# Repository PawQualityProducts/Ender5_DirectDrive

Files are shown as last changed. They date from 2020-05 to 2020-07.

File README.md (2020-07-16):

# DirectDrive Mount for Creality Ender 5+ (5 Pro and 5)
By Paul.Haines@PawQualityProducts.co.uk

## Design Considerations
This is a Simple Direct Drive Mount originally designed for the Creality Ender 5+, but may also be compatible with the Ender 5 and Ender 5 Pro.

It was developed to:
* Improve injection of filament into the Hot-End by mounting the Extruder Drive close to the Hot-End
* Provide a more even balance for the Print-Head by utilising the Extruder Drive Stepper Motor as a counter-weight to the Hot-End assembly. This was done by making use of the space between the Print-Head Assembly and Carriage Rollers
<br/>
<b>Disclaimer</b><br/>
<i>The 3D print models, STL files, instructions etc. contained in this repository may be used freely but at your own risk.<br/> No liability will be accepted for damage or loss resulting from the use of any files or information contained in this repository.</i>

## To build the Direct Drive Mount you will need:
1. The Direct Drive Mount STL files<br/>
Two versions are available:
- <a href="https://github.com/PawQualityProducts/Ender5_DirectDrive/blob/master/DirectDriveMount_Ender5_Plus.stl">Ender 5+ version (with BLTouch)</a> <br/>
- <a href="https://github.com/PawQualityProducts/Ender5_DirectDrive/blob/master/DirectDriveMount_Ender5_NoBLTouch.stl">Ender 5x version (without BLTouch)</a> <br/>

A <a href="https://github.com/hainesyp/Ender5Plus_DirectDrive/blob/master/DirectDriveMount_Ender5_x_Guide.stl">Filament Guide</a> is also provided. <i>NB: An M3 (3mm x 20mm) bolt and nut are required to attach the Guide to the Mount</i>
<br/>
<br/>
<b><i>Build with standard settings with Full Support enabled (there's only a bit of support)</i></b><br/>
<br/>
2. <a href="https://www.amazon.co.uk/gp/product/B07SY745CF/ref=ppx_yo_dt_b_asin_title_o03_s00?ie=UTF8&psc=1">WINSINN Ender Aluminum Dual Extrusion Drive Feed</a> <br/>
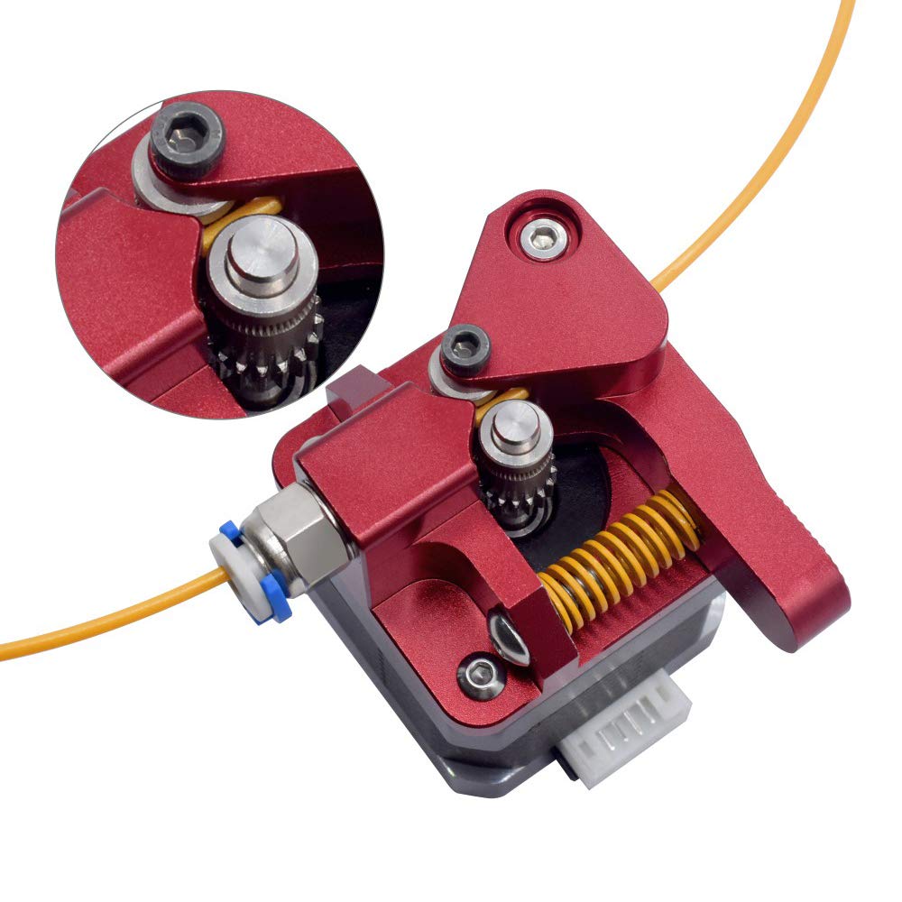
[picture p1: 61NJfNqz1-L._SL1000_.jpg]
 <br/>
<i>NB: If you are installing the WINSINN Extruder Drive Feed assembly as part of this Mod, then I recommend you install it first, and <b>re-calibrate the E-Step settings on your printer</b>, to ensure it's operating correctly before proceeding with the rest of the Mod</i>
<br/>
<br/>
3. Cable Extender ( used in Reprap 3D Printers CNC Machines): <br/>
<a href="https://www.amazon.co.uk/gp/product/B0728J6QTG/ref=ppx_yo_dt_b_asin_image_o00_s00?ie=UTF8&psc=1">UEETEK Bipolar Stepper Motor Cable for NEMA 17</a>  <br/>
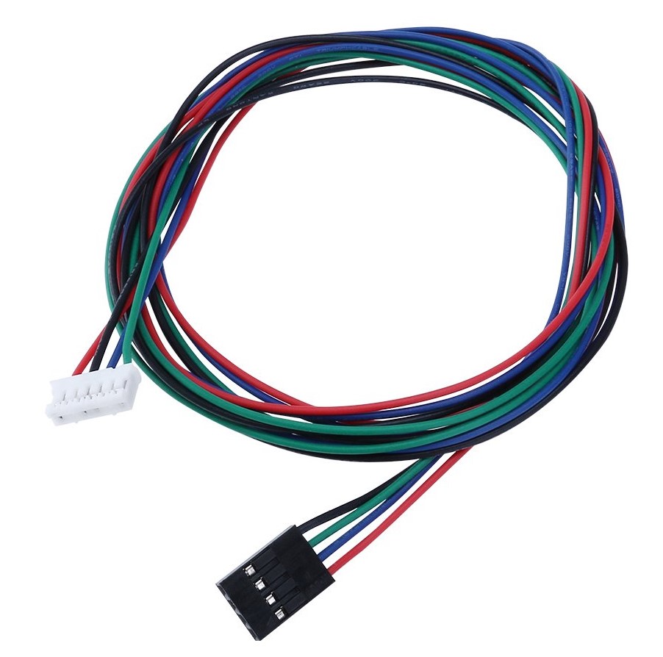
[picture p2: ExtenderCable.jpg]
 <br/>
<br/>
Additionally, I used a Male-To-Male <a href="https://www.amazon.co.uk/Elegoo-120pcs-Multicolored-Breadboard-arduino-colorful/dp/B01EV70C78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">Dupont Cable</a> to make the connection between your stepper motor cable and the extended stepper motor cable<br/>
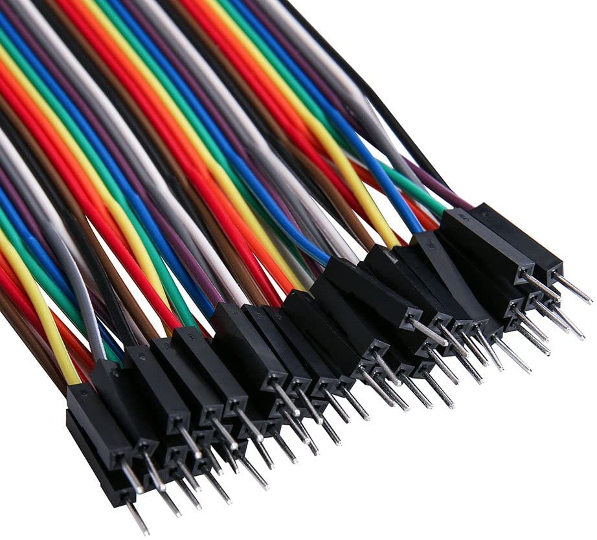
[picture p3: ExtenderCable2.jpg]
 <br/>

4. 80mm of Bowden Tube (Capricorn Tubing recommended) <br/>
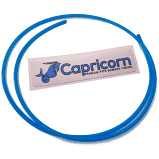
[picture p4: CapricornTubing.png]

<br/>

## To mount onto the print-head:
<table>
  <tr>
    <td>
      <h3>Step 1</h3>
      <p>Heat the Hot-End to ~190 degrees then Remove the Bowden Tube from the Hot-End</p>
    </td>
    <td>&nbsp;</td>
  </tr>
  <tr>
    <td>
      <h3>Step 2</h3>
      <p>Allow the hot-end to cool then remove the Bowden Tube Connector from the Hot-End</p>
    </td>
    <td>&nbsp;</td>
  </tr>
  <tr>
    <td>
      <h3>Step 3</h3>
      <p>Release the tension on the X Drive belt, then remove to top two rollers from the Hot-End carriage<br/>
        <i>NB: It is recommended that you position the Hot-Bed so that the Print-Head carriage can be supported while the Direct Drive Mount is attached. It's also advisable to protect your Hot-Bed surface during the mounting process (eg. especially when attaching the drive stepper motor)</i>
      </p>
    </td>
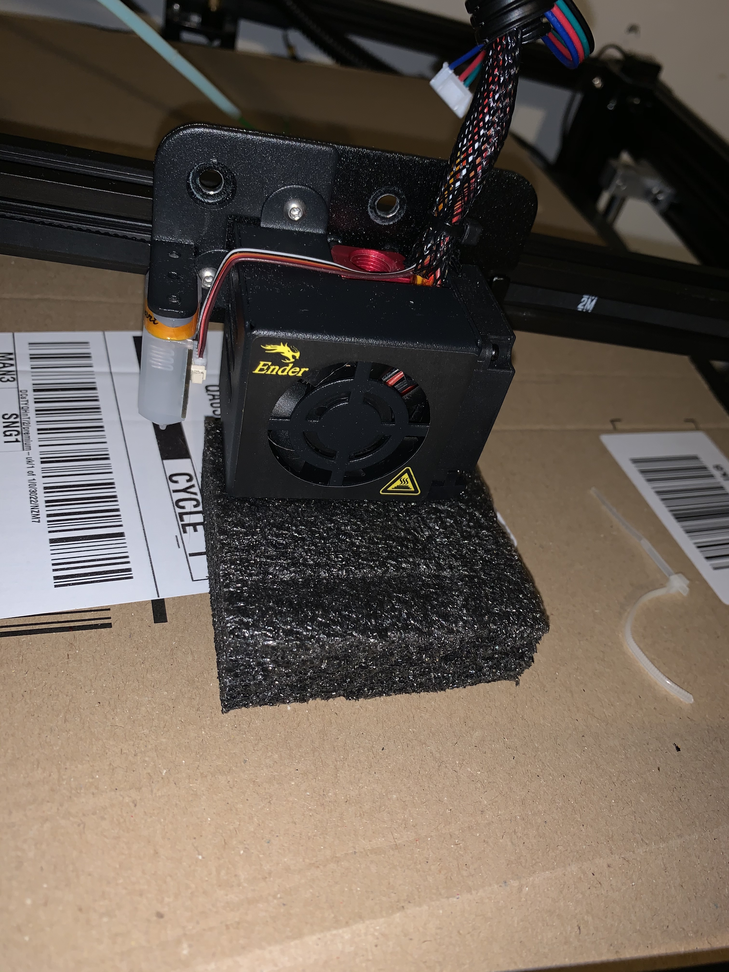
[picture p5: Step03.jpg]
    <td></td>
  </tr>
  <tr>
    <td>
      <h3>Step 4</h4>
      <p>Insert the two roller-spacers into the holes on the Direct Drive Mount (Image Step 4 below) ensuring they are flush with the side that will make contact with the Print-Head mount</p>
    </td>
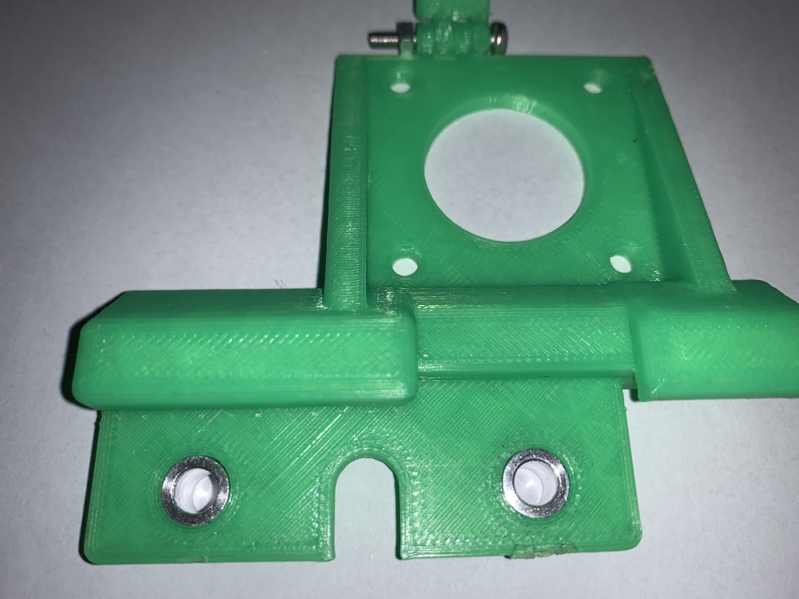
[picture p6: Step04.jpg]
    <td></td>
  </tr>
  <tr>
    <td>
      <h3>Step 5</h4>
      <p>Hook the Direct Drive Mount onto the Hot-End carriage, aligning the roller holes</p>
    </td>
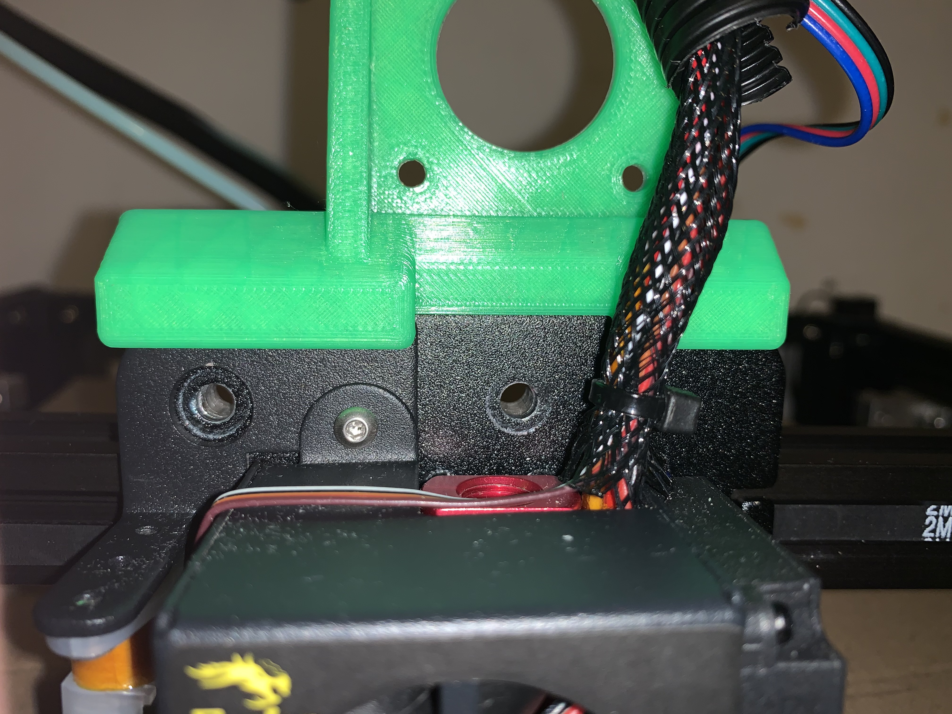
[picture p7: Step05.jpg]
    <td></td>
  </tr>
  <tr>
    <td>
      <h3>Step 6</h4>
      <p>Re-mount the Hot-End carriage, and attach the rollers</p>
    </td>
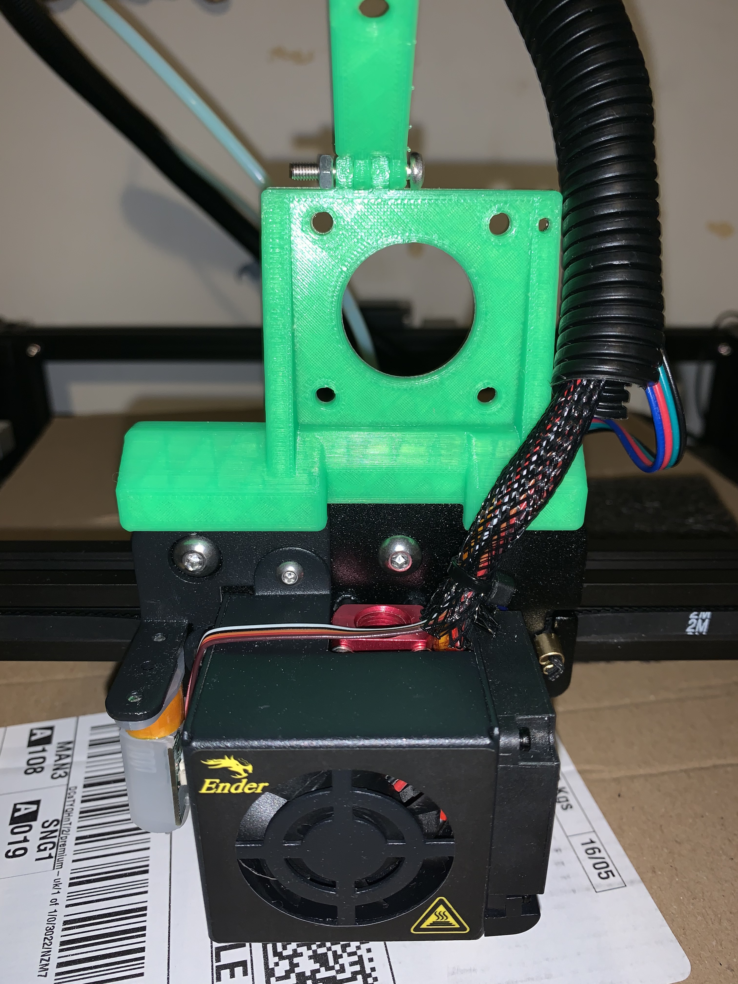
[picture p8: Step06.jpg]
    <td></td>
  </tr>
  <tr>
    <td>
      <h3>Step 7</h4>
      <p>Attach the Bowden Tube connector to the Hot-End</p>
    </td>
    <td>&nbsp;</td>
  </tr>
  <tr>
    <td>
      <h3>Step 8</h4>
      <p>Heat the Hot-End to ~190 Degrees then push the 80mm length of Bowden Tube into the Hot-End as far as it will go.</p>
    </td>
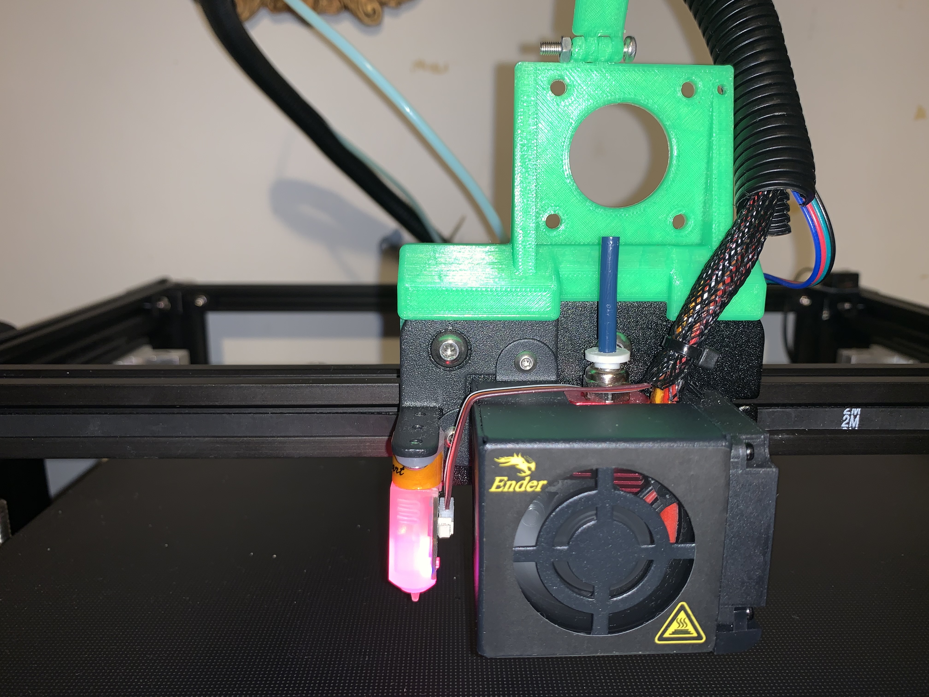
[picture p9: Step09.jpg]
    <td></td>
  </tr>
  <tr>
    <td>
      <h3>Step 9</h4>
      <p>Insert the other end of the Tube into the Extruder Drive Assembly so that the Bowden Tube connects the Hot-End and Extruder Assembly</p>
      <p><i>Note that the Extruder Drive Assembly should be mounted upside down (180 degress from it's original orientation), but should otherwise be assembled exactly as it was before. This Mod does not change the function of the Extruder Drive Assembly itself, just it's mounting location and orientation.</i></p>
    </td>
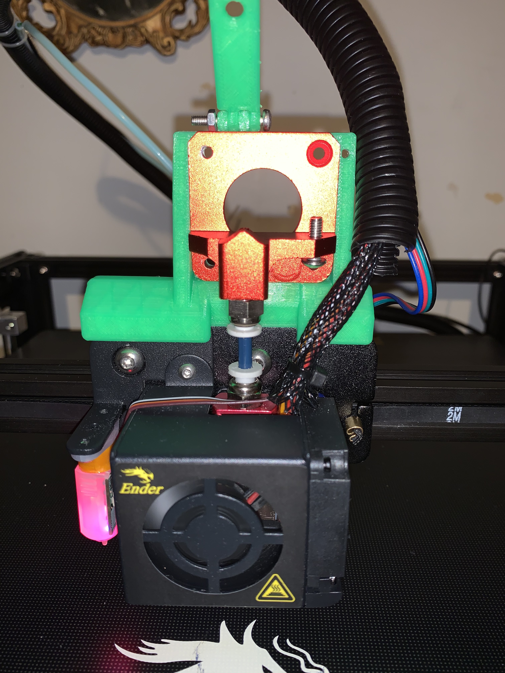
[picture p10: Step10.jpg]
    <td></td>
  </tr>
  <tr>
    <td>
      <h3>Step 10</h4>
      <p>Mount the Extruder Driver Stepper Motor and Extruder Drive Assembly onto the Direct Drive Mount, and complete Extruder Drive Assembly</p>
    </td>
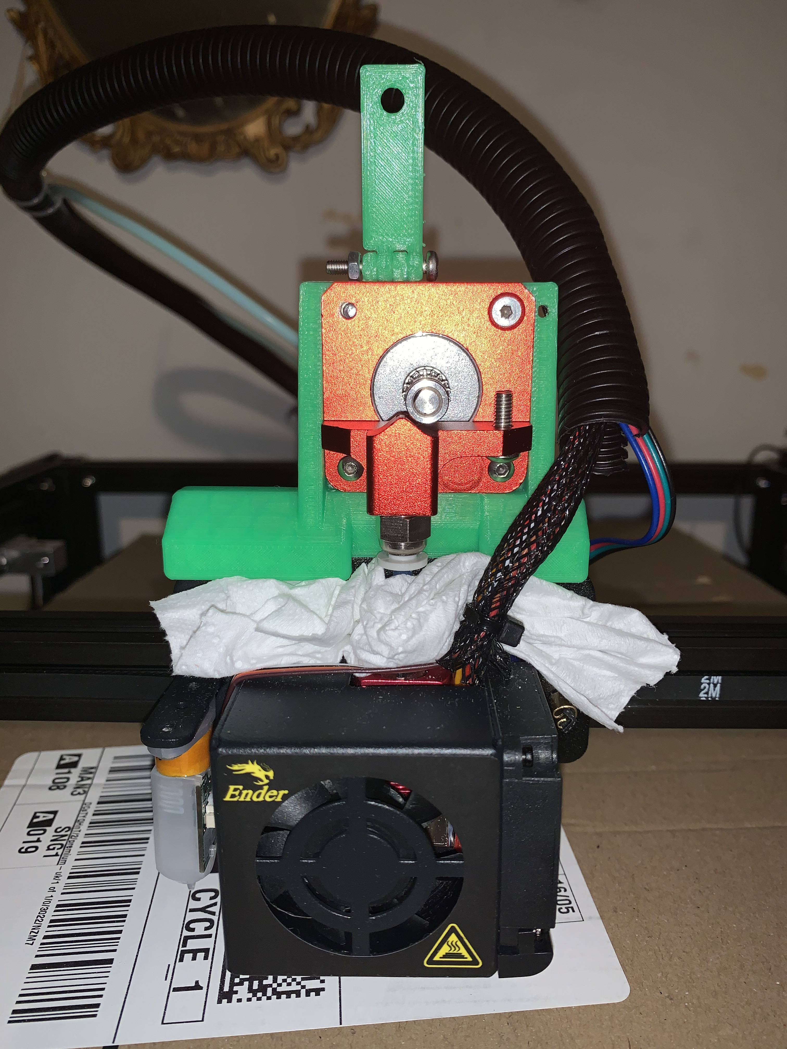
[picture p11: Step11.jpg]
    <td></td>
  </tr>
  <tr>
    <td>
      <h3>Step 11</h4>
      <p>Extend the Extruder drive Stepper Motor cable and connect</br>
    <i>NB: I used <a href="https://www.amazon.co.uk/gp/product/B01EV70C78/ref=ppx_yo_dt_b_asin_title_o01_s00?ie=UTF8&psc=1">Dupont Wire Male to Male Connector Cables</a> to connect the UEETEK Bipolar Stepper Motor Cable to the existing stepper motor cable so no cutting or soldering was required</i> <br/></br>
    <b>When extending Extruder drive Setpper Motor cable, be sure to reconnect correctly (ie. wire it as originally wired). You should NOT need to switch any wires. If your drive appears to be running in the wrong direction, then you have most-likely mounted the Extruder Drive Assembly incorrectly. The Extruder Drive Assembly should be mounted upside down (ie. 180 degrees from it's original orientation) but should otherwise be assembled in exactly the same way it was before. </b>
  </p>
    </td>
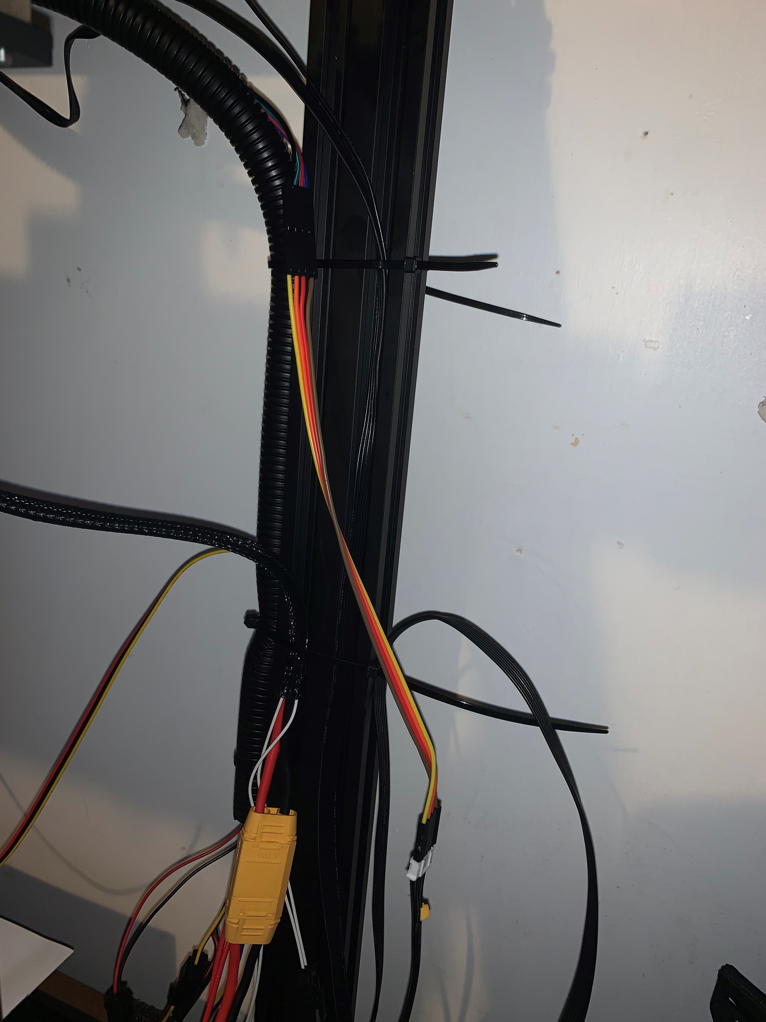
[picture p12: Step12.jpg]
    <td></td>
  </tr>
  <tr>
    <td>
      <h3>Step 12</h4>
      <p>Re-tension the X Drive Belt then test</br></p>
    </td>
    <td>&nbsp;</td>
  </tr>
</table>

## Configuration
The Extuder E-Steps were calibrated when I installed the WINSINN Ender Dual Gear Extruder;<br />
However, no other printer, extruder or slicer configuration setting changes have been required.

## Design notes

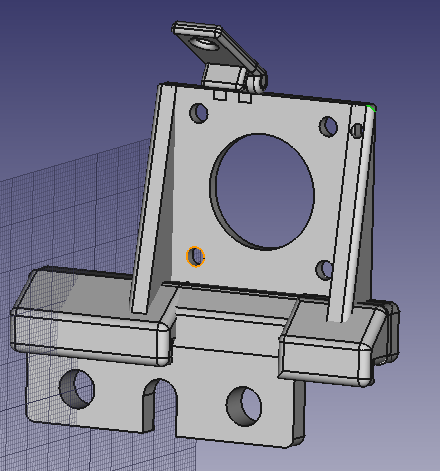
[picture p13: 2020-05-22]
Image.png

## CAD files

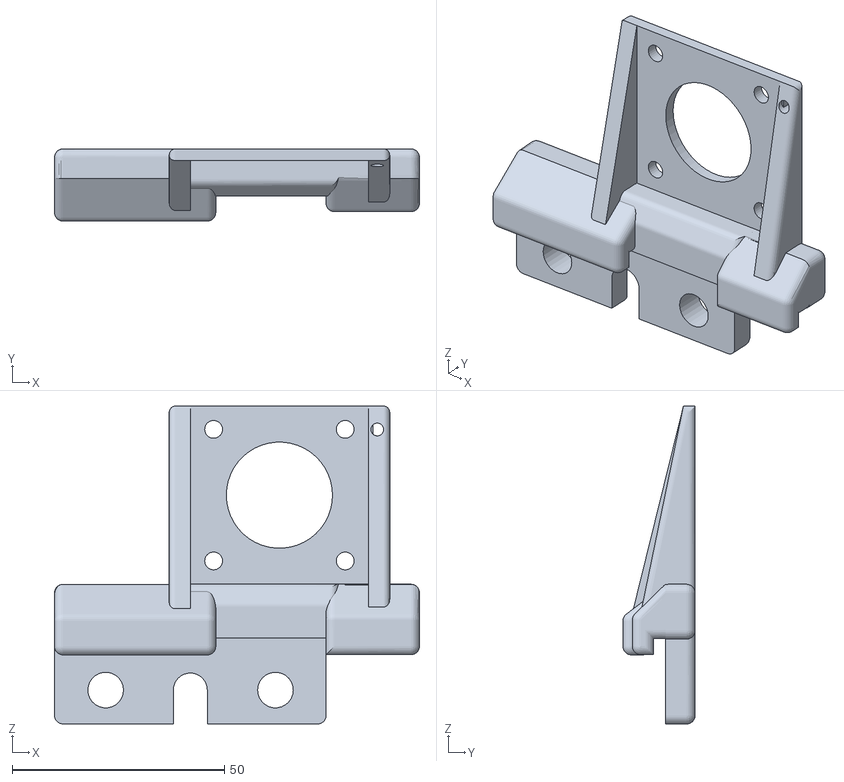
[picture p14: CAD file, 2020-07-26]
DirectDriveAsSolid2.stl
86.0 x 17.0 x 74.9

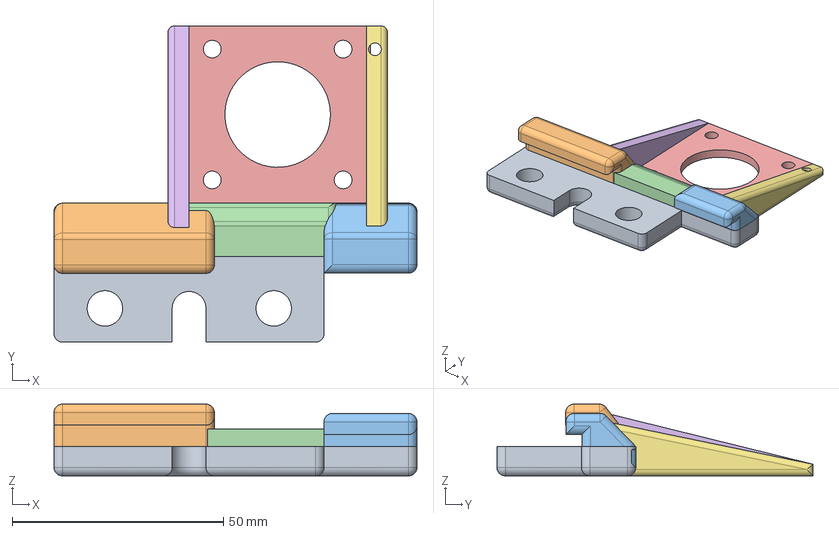
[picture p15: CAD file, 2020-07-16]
DirectDriveMount_Ender5_Plus.FCStd
86.0 x 74.9 x 17.0 mm
MainBody
LeftClamp
RightClamp
Centre
BackPlate
LeftSupport
RightSupport

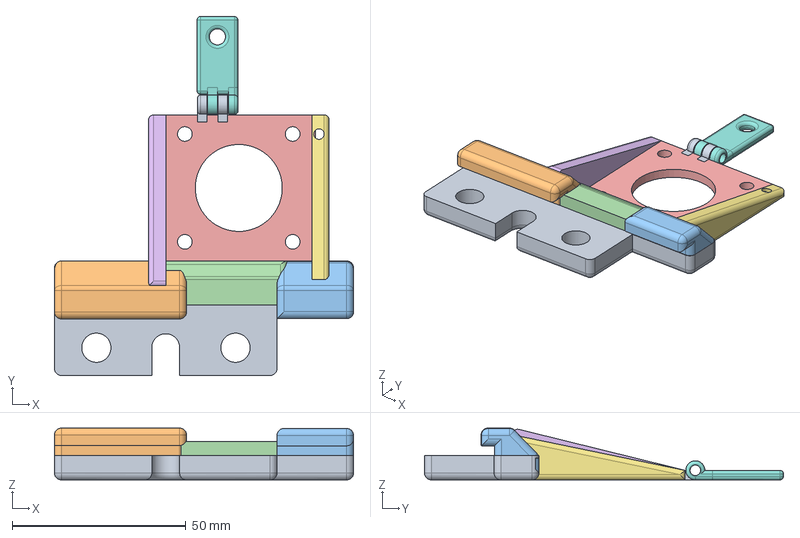
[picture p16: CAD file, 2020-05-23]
DirectDriveMount_Ender5_NoBLTouch.FCStd
86.0 x 103.2 x 14.9 mm
MainBody
LeftClamp
RightClamp
Centre
BackPlate
LeftSupport
RightSupport
Guide
BackplateHinges

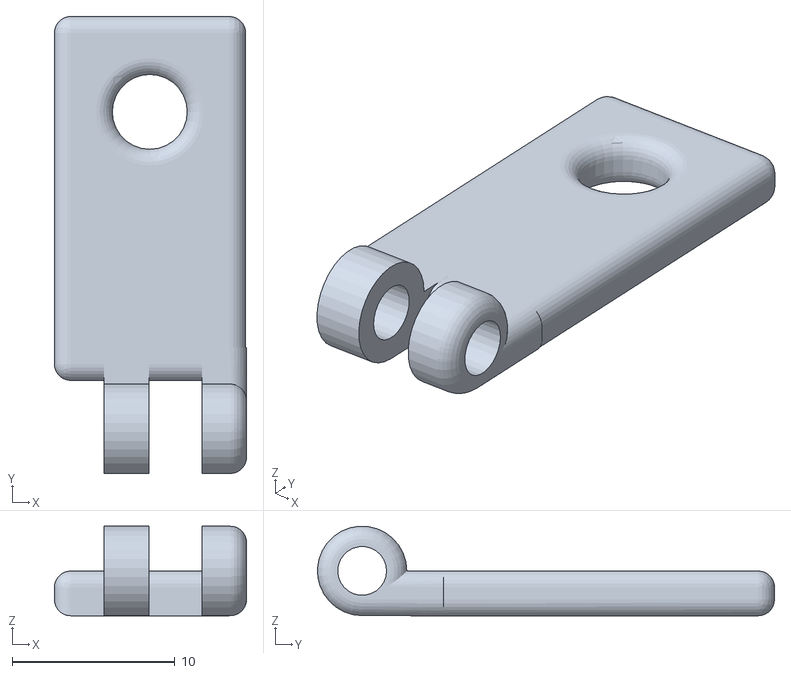
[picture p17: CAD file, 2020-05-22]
DirectDriveMount_Ender5_x_Guide.stl
11.8 x 28.1 x 5.50

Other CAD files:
DirectDriveAsSolid.stl
DirectDriveMount_Ender5_NoBLTouch.stl
DirectDriveMount_Ender5_Plus.stl

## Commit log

2020-05-22 Initial Commit - V5.1 and 5.2
    [DirectDriveMount5.1.FCStd, DirectDriveMount5.1.stl, DirectDriveMount5.1_Guide.stl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]
2020-05-22 Capricorn Tubing
2020-05-23 Created Ender 5 specific Version
    [DirectDriveMount5.1.FCStd, DirectDriveMount5.1.stl, DirectDriveMount5.2.FCStd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]
2020-07-16 Added new Cable Extender image
    [DirectDriveMount_Ender5_Plus.FCStd]
2020-07-26 added cleaned up slolid models
    [DirectDriveAsSolid.stl, DirectDriveAsSolid2.stl]
